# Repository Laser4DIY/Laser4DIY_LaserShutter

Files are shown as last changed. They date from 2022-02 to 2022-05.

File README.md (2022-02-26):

# LASER4DIY Laser Shutter

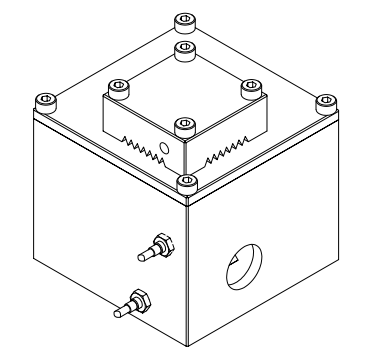
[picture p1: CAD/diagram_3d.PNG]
Laser4DIY Laser Shutter - 3D view

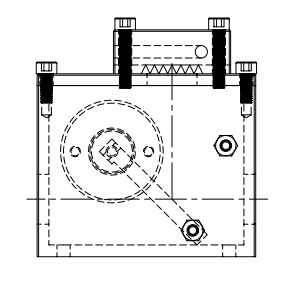
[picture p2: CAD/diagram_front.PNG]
Laser4DIY Laser Shutter - front view


This is the repository is part of the [Laser4DIY project](http://www.laser4diy.org/).

## Description 

The laser shutter was designed for CO2 glass tube laser sources typically used in laser cutters, with a power of no more than 50W. The design includes a beam dump which takes up the laser power when the laser is active but the shutter is closed. The actual maximum power depends on how this block is cooled. Please add a heat sink or - even better - active cooling, depending on your requirements. The shutter lid itself is made of copper which has a high reflectivity at the wave length of ~10µm. For other wave lengths this is design cannot be used.

For a laser shutter to be effective, it has to be integrated into the machine safety concept. The electronics circuit that is included in this documentation can only serve as an example and has to be adapted to your needs.

Please note that this documentation is distributed without any express or implied warranty. Use it at your own risk. Please also read the details of the CERN-OHL license.

## License

This hardware documentation is licensed under CERN-OHL-P v2.

---

Copyright FabLab München e.V. 2021.

Laser4DIY is sponsored by the Federal Ministry of Education and Research

This source describes Open Hardware and is licensed under the CERN-OHL-P v2

You may redistribute and modify this documentation and make products using it 
under the terms of the CERN-OHL-P v2 (https:/cern.ch/cern-ohl).
This documentation is distributed WITHOUT ANY EXPRESS OR IMPLIED WARRANTY, 
INCLUDING OF MERCHANTABILITY, SATISFACTORY QUALITY AND FITNESS FOR A  PARTICULAR 
PURPOSE. Please see the CERN-OHL-P v2 for applicable conditions

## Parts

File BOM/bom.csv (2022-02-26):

No. | Artikel | Hersteller | Bezugsquelle | Bestellnummer | Stk. | Preis (ca) | Summe
1 | Ber hrungsloser Sicherheitsschalter | Pilz | RS Components | 619-2818 | 1 | 60 | 60
2 | PNOZ X3, 2-Kanal Sicherheitsrelais | Pilz | RS Components | 245-1848 | 0 | 220 | 0
3 | PNOZ s3, 2-Kanal Sicherheitsrelais | Pilz | RS Components | 156-083 | 2 | 150 | 300
4 | Drehmagnet D34 | Kuhnke | B rklin | 27G184 | 1 | 140 | 140
5 | PSEN Kabel Gerade | Pilz | Pilz | 533111 | 1 | 10 | 10
6 | Induktiver Sensor Schlieáer IM04-0B6PS-ZU1 | Sick | RS Components | 209-3201 | 1 | 85 | 85
7 | Induktiver Sensor ffner IM04-0B6PO-ZU1 | Sick | RS Components | 209-3198 | 1 | 85 | 85
8 | Shutter Fr steile | custom |  |  | 1 | 200 | 200
 |  |  |  |  |  | Summe | 880

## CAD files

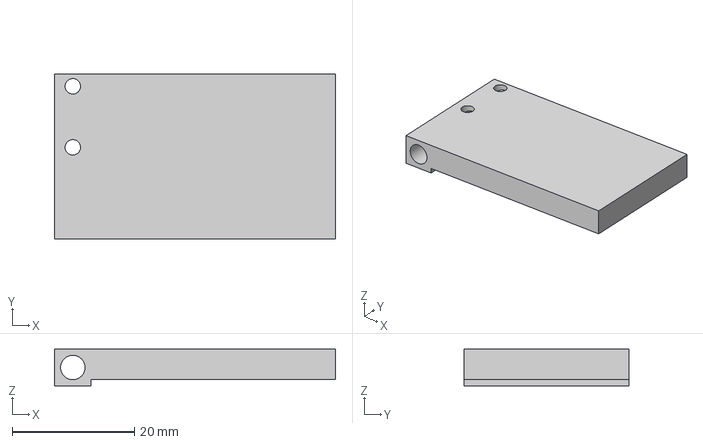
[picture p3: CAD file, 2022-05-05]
CAD/STEP/Fahne.step
46.0 x 27.0 x 6.00 mm

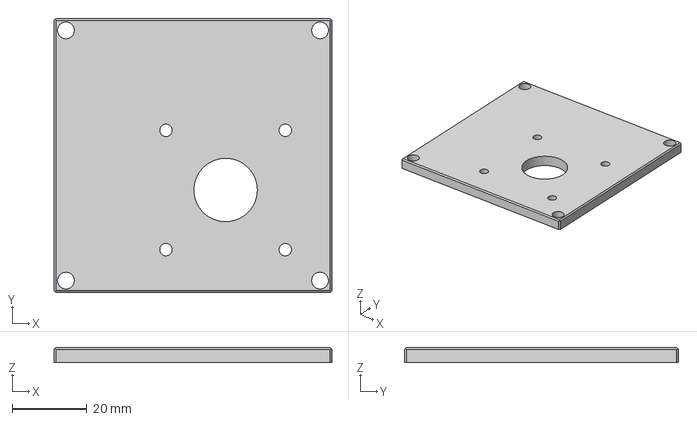
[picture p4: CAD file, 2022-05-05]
CAD/STEP/Deckel.step
74.5 x 73.5 x 4.00 mm

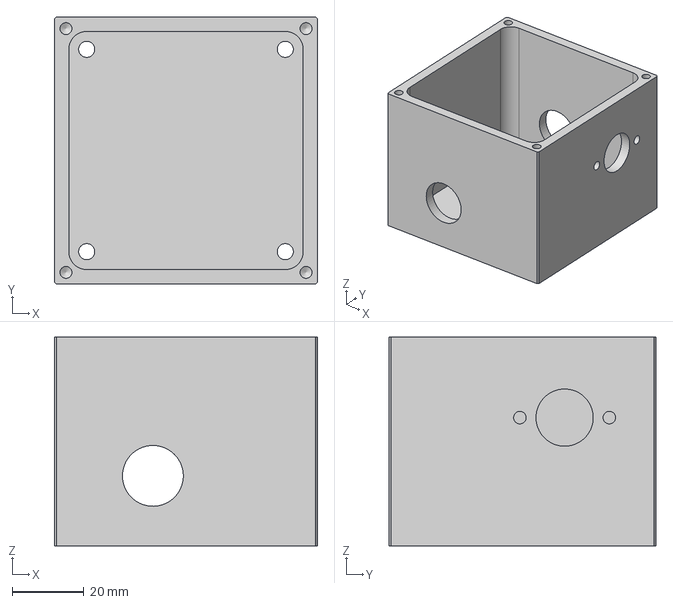
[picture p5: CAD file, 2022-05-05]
CAD/STEP/Gehaeuse.step
73.5 x 74.5 x 58.3 mm

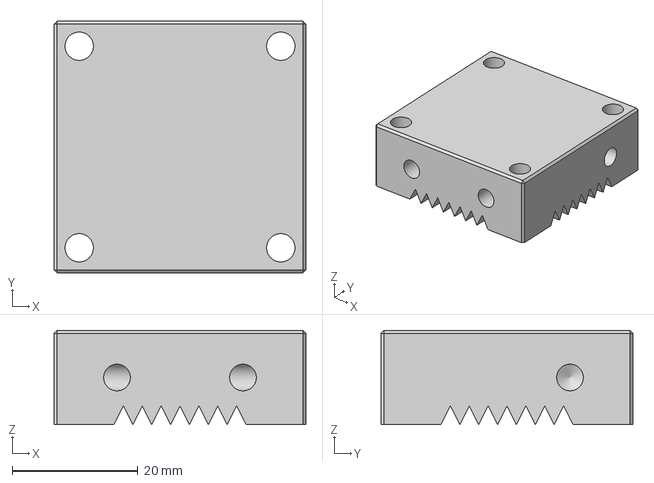
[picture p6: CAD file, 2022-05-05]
CAD/STEP/Kuehlung.step
40.0 x 40.0 x 15.0 mm

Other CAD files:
CAD/Shutter.f3z

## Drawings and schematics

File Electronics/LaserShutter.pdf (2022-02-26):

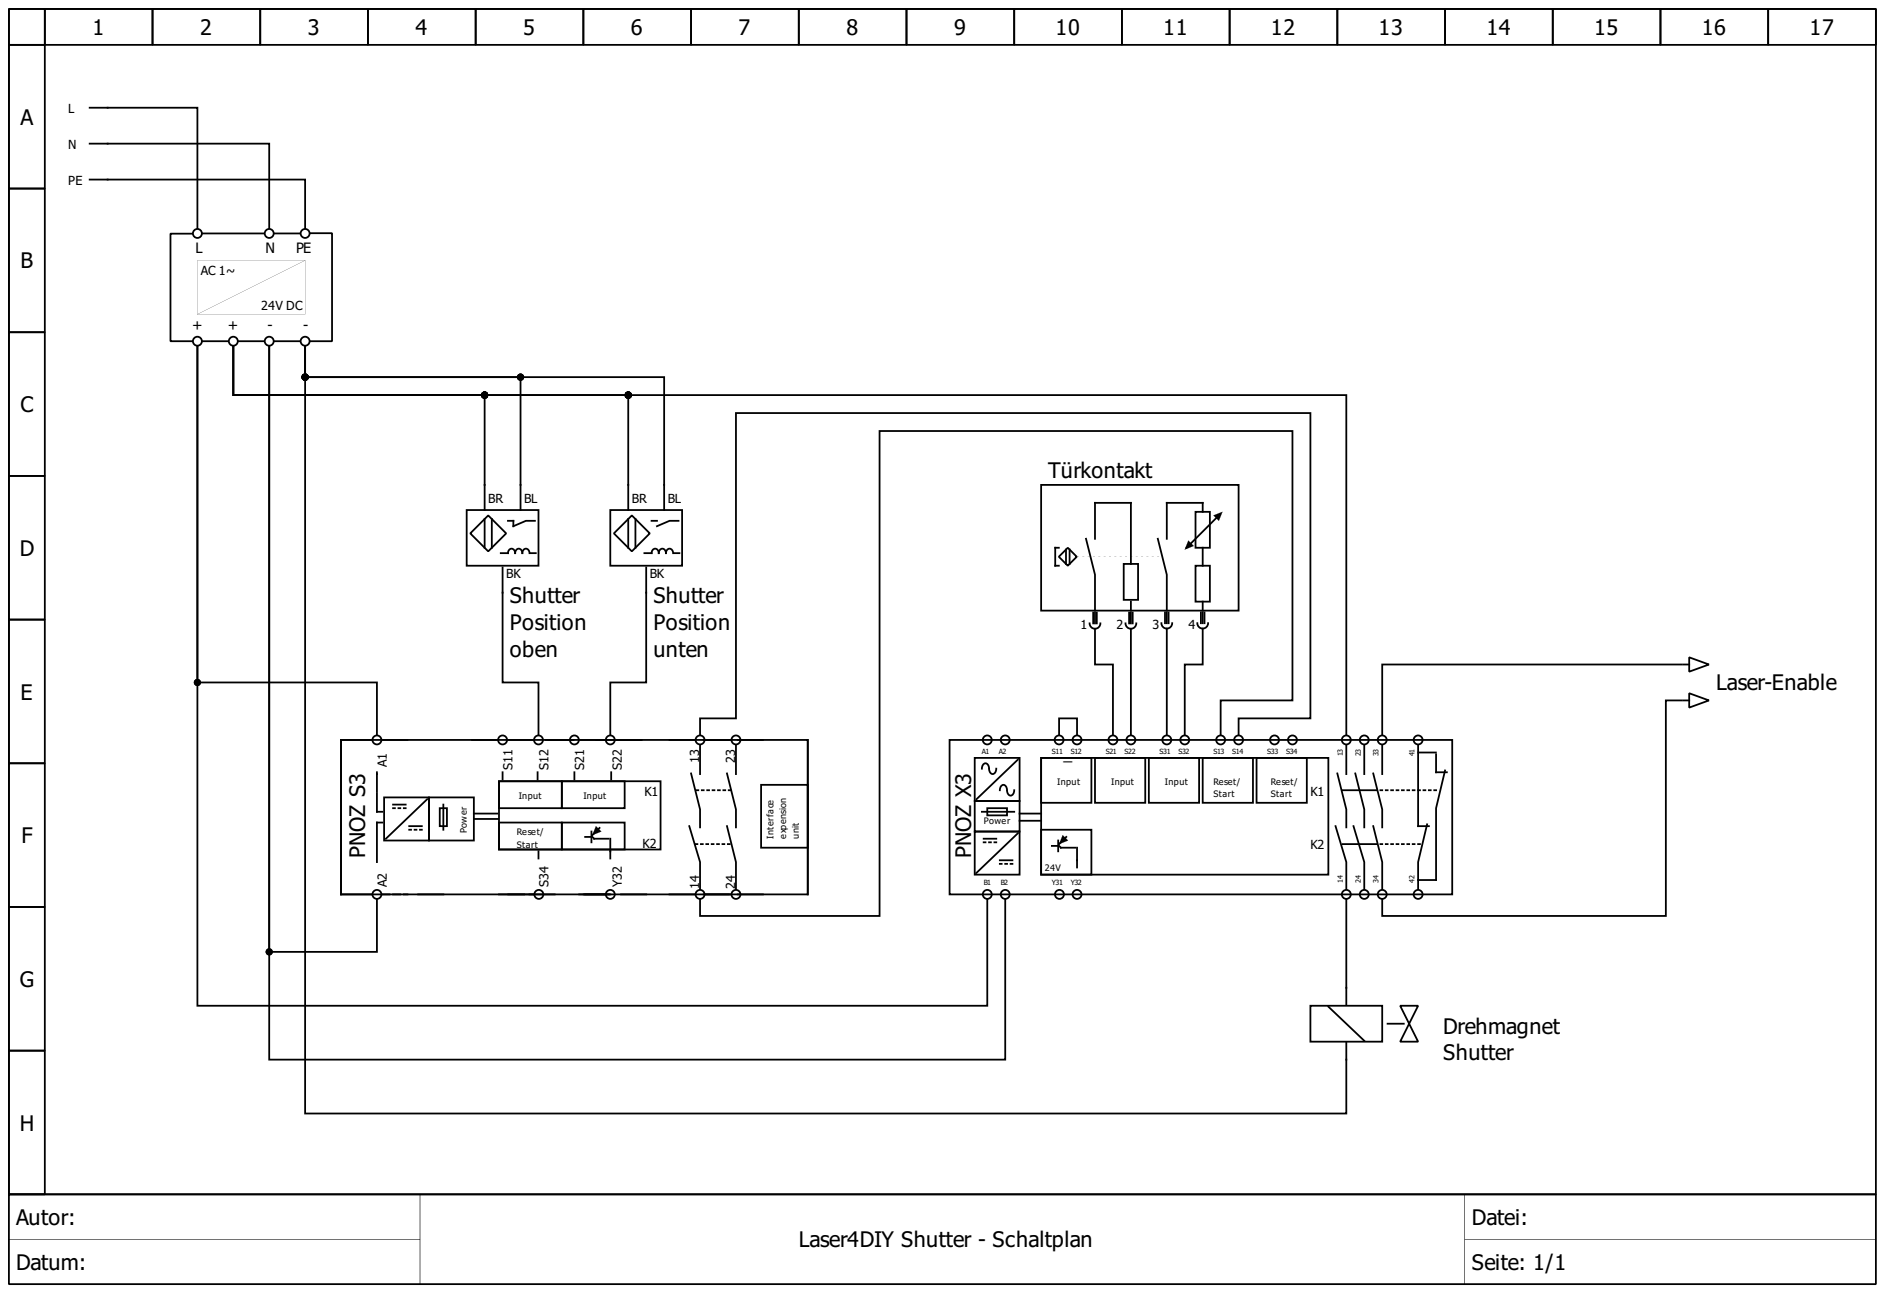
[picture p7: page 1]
Input; Reset/ Start; Interface; expension; unit; Power; Reset/; Start; Drehmagnet Shutter; Türkontakt; Shutter Position unten; Shutter Position oben; Laser-Enable

Autor: | Laser4DIY Shutter - Schaltplan | Datei:
Datum: | | Seite: 1/1

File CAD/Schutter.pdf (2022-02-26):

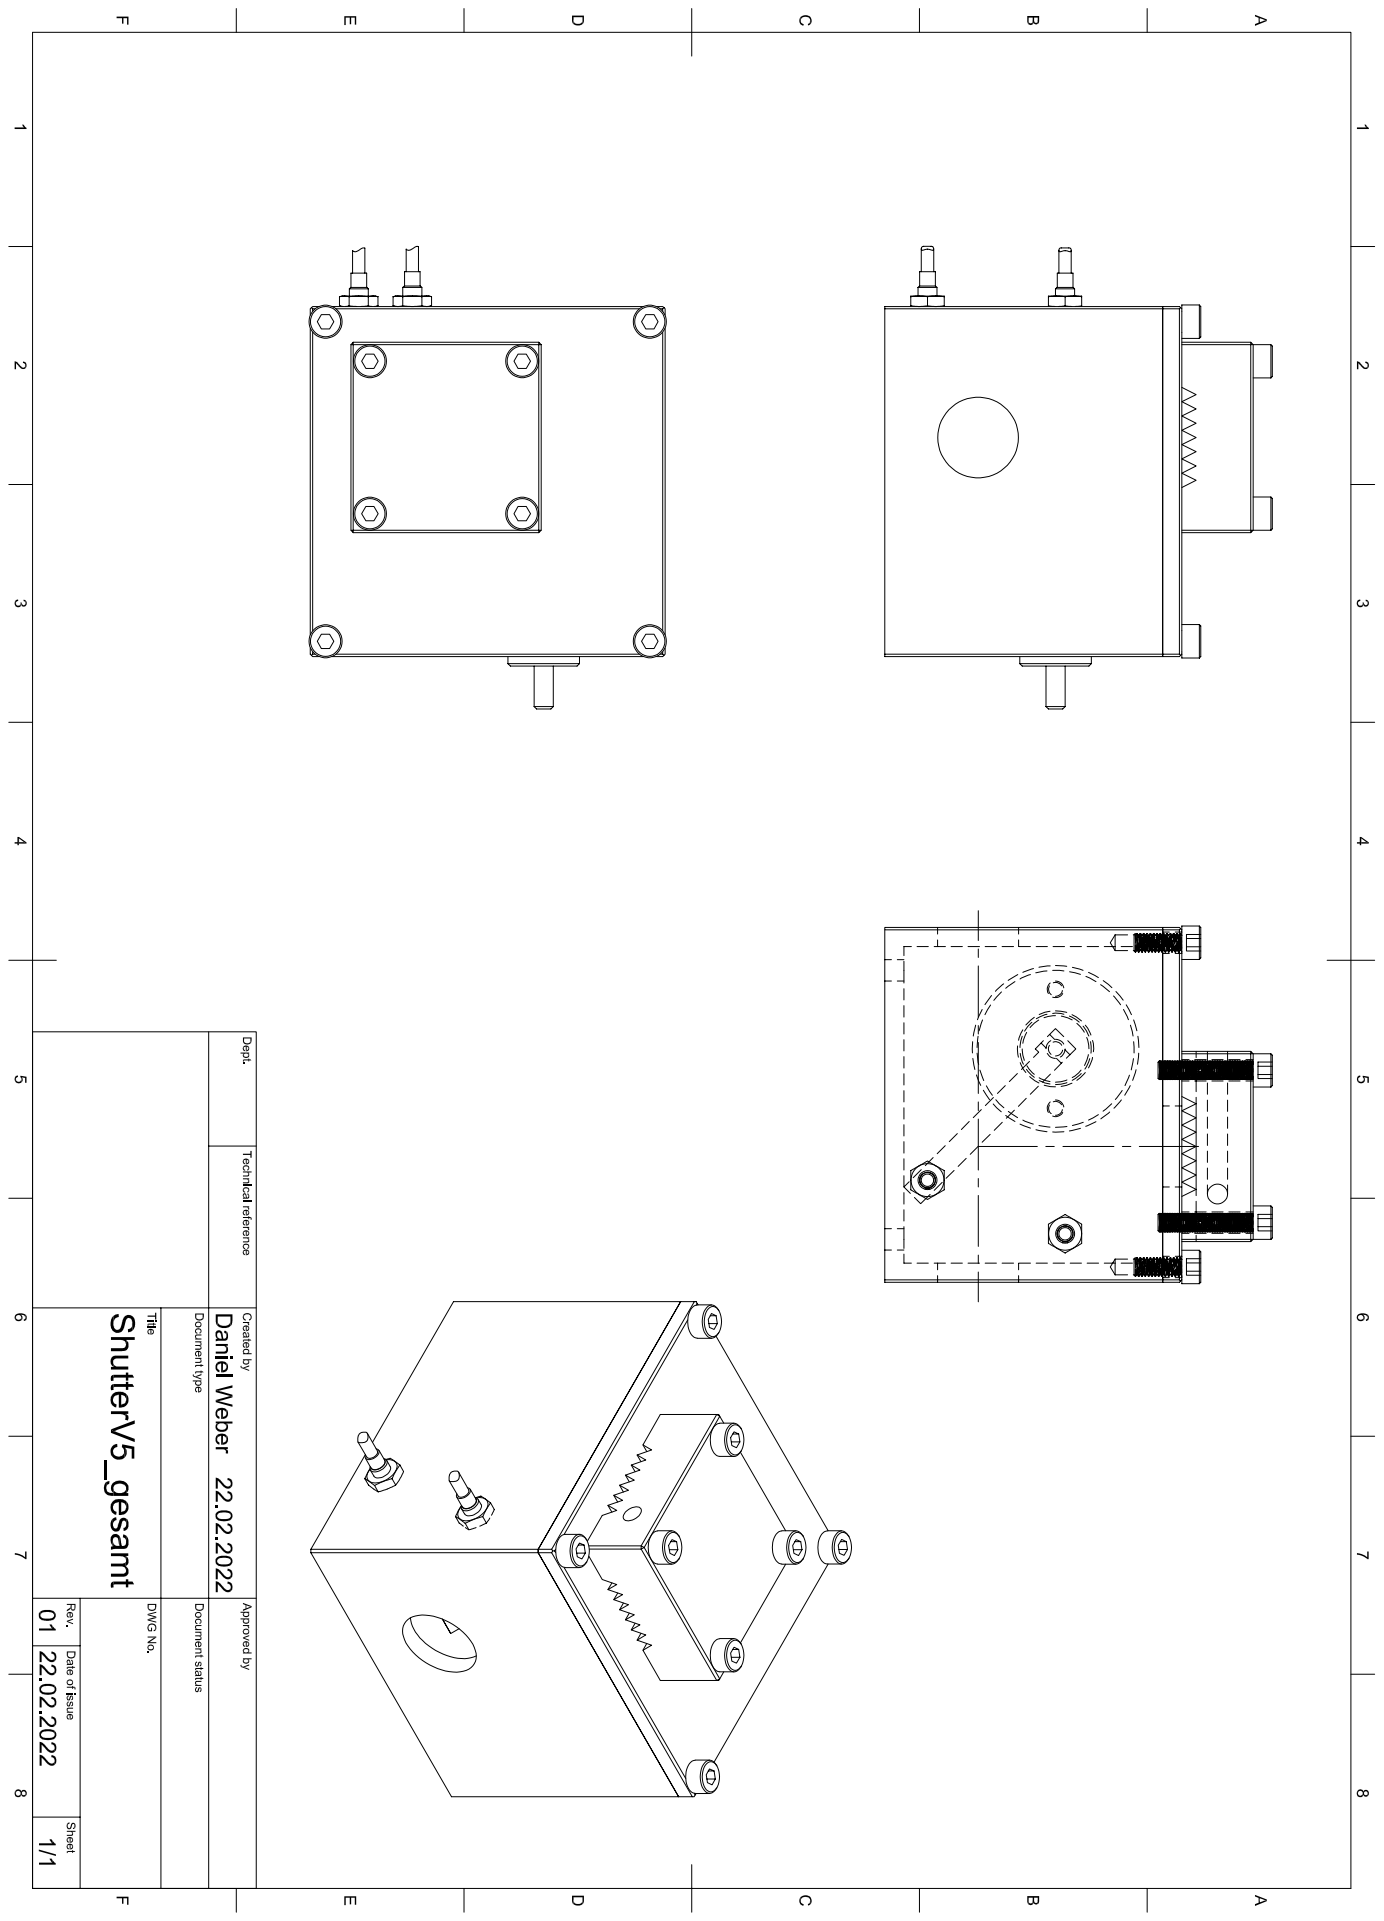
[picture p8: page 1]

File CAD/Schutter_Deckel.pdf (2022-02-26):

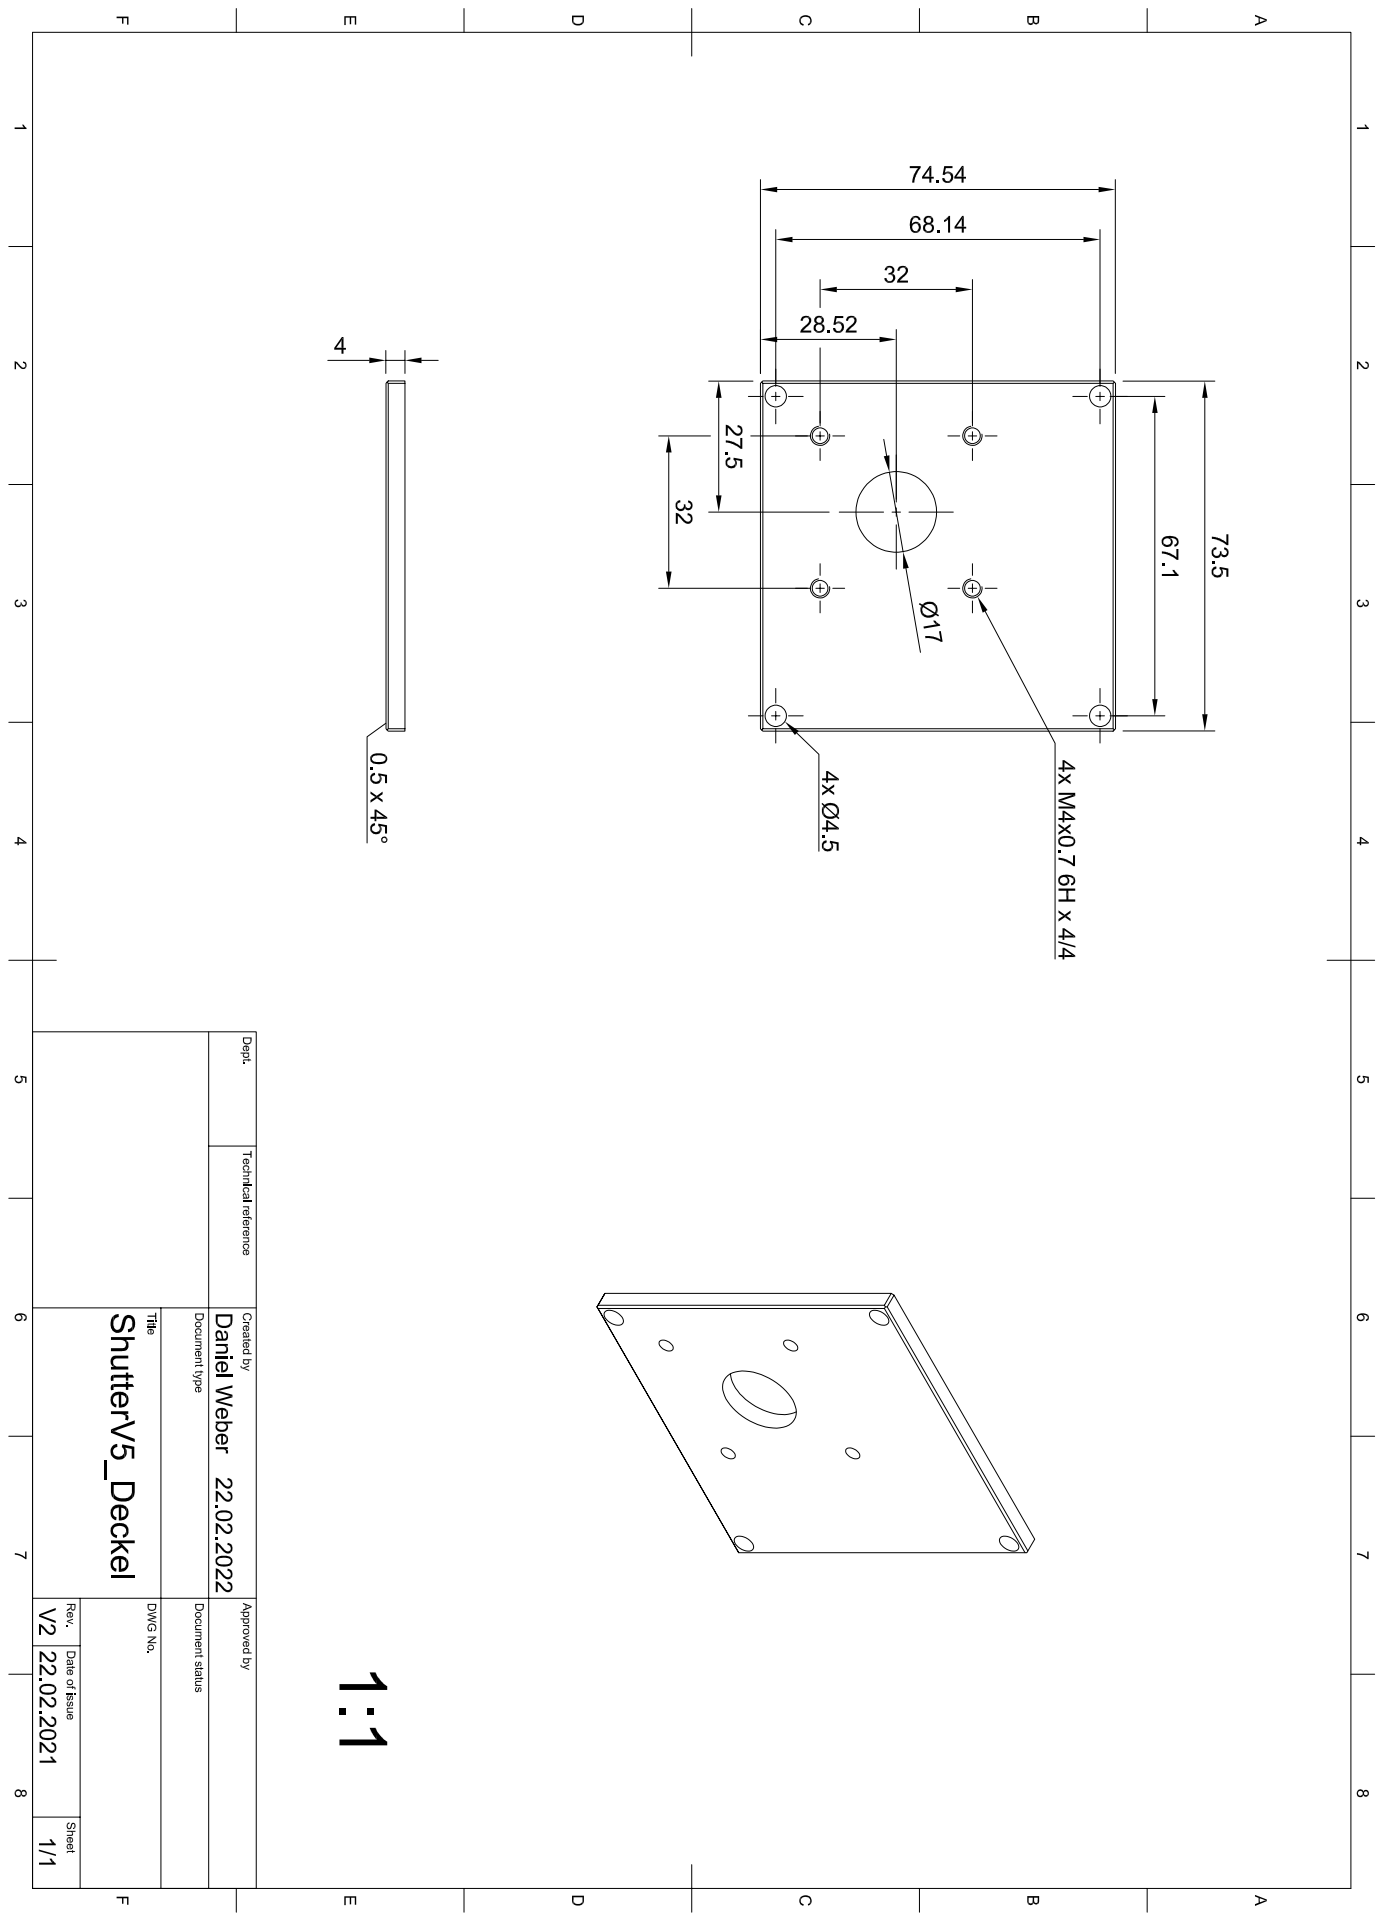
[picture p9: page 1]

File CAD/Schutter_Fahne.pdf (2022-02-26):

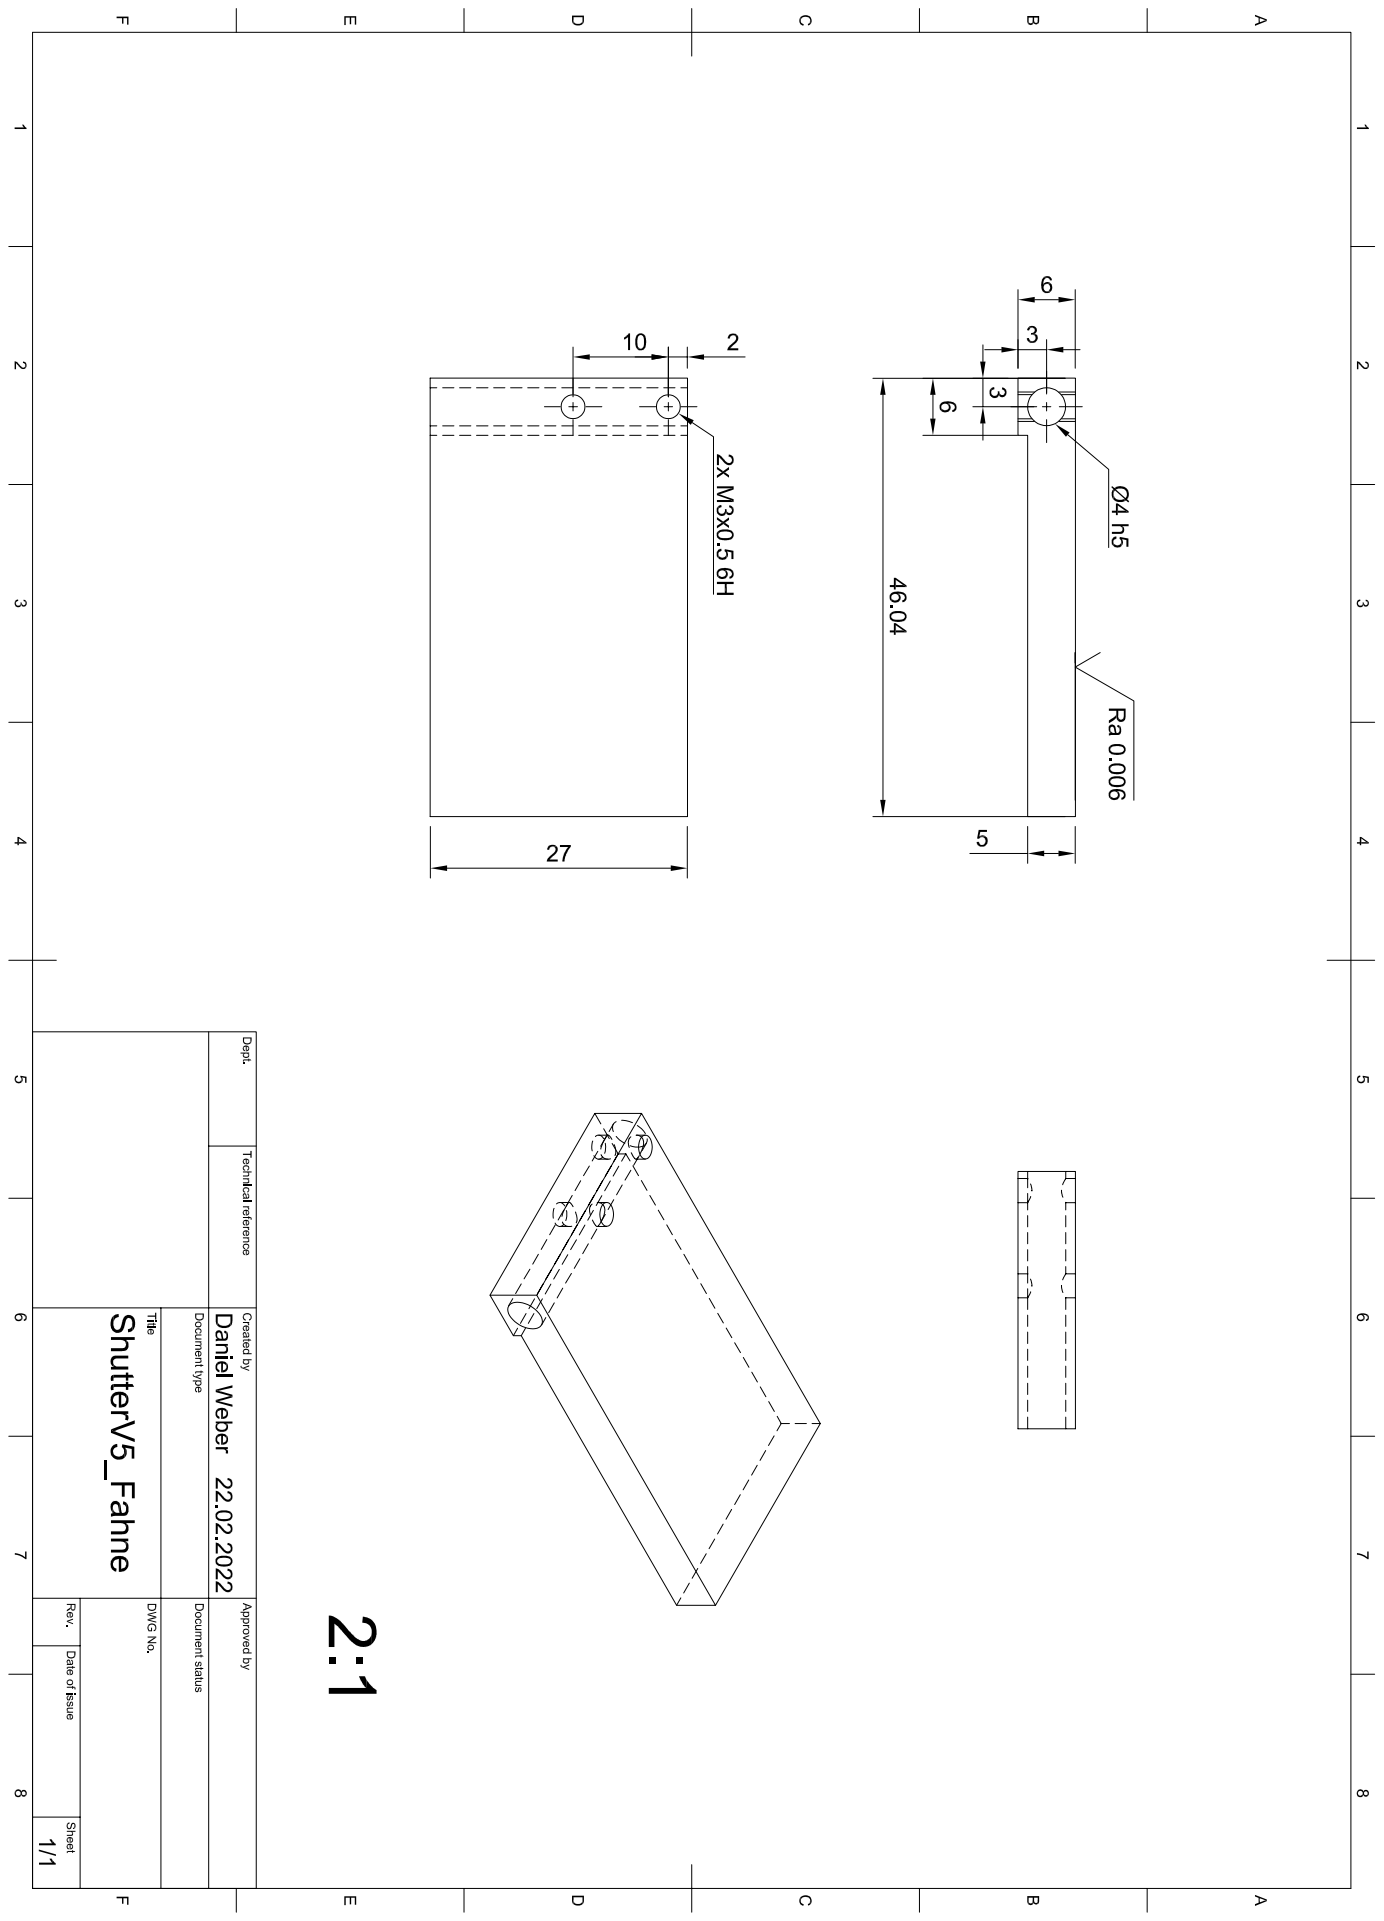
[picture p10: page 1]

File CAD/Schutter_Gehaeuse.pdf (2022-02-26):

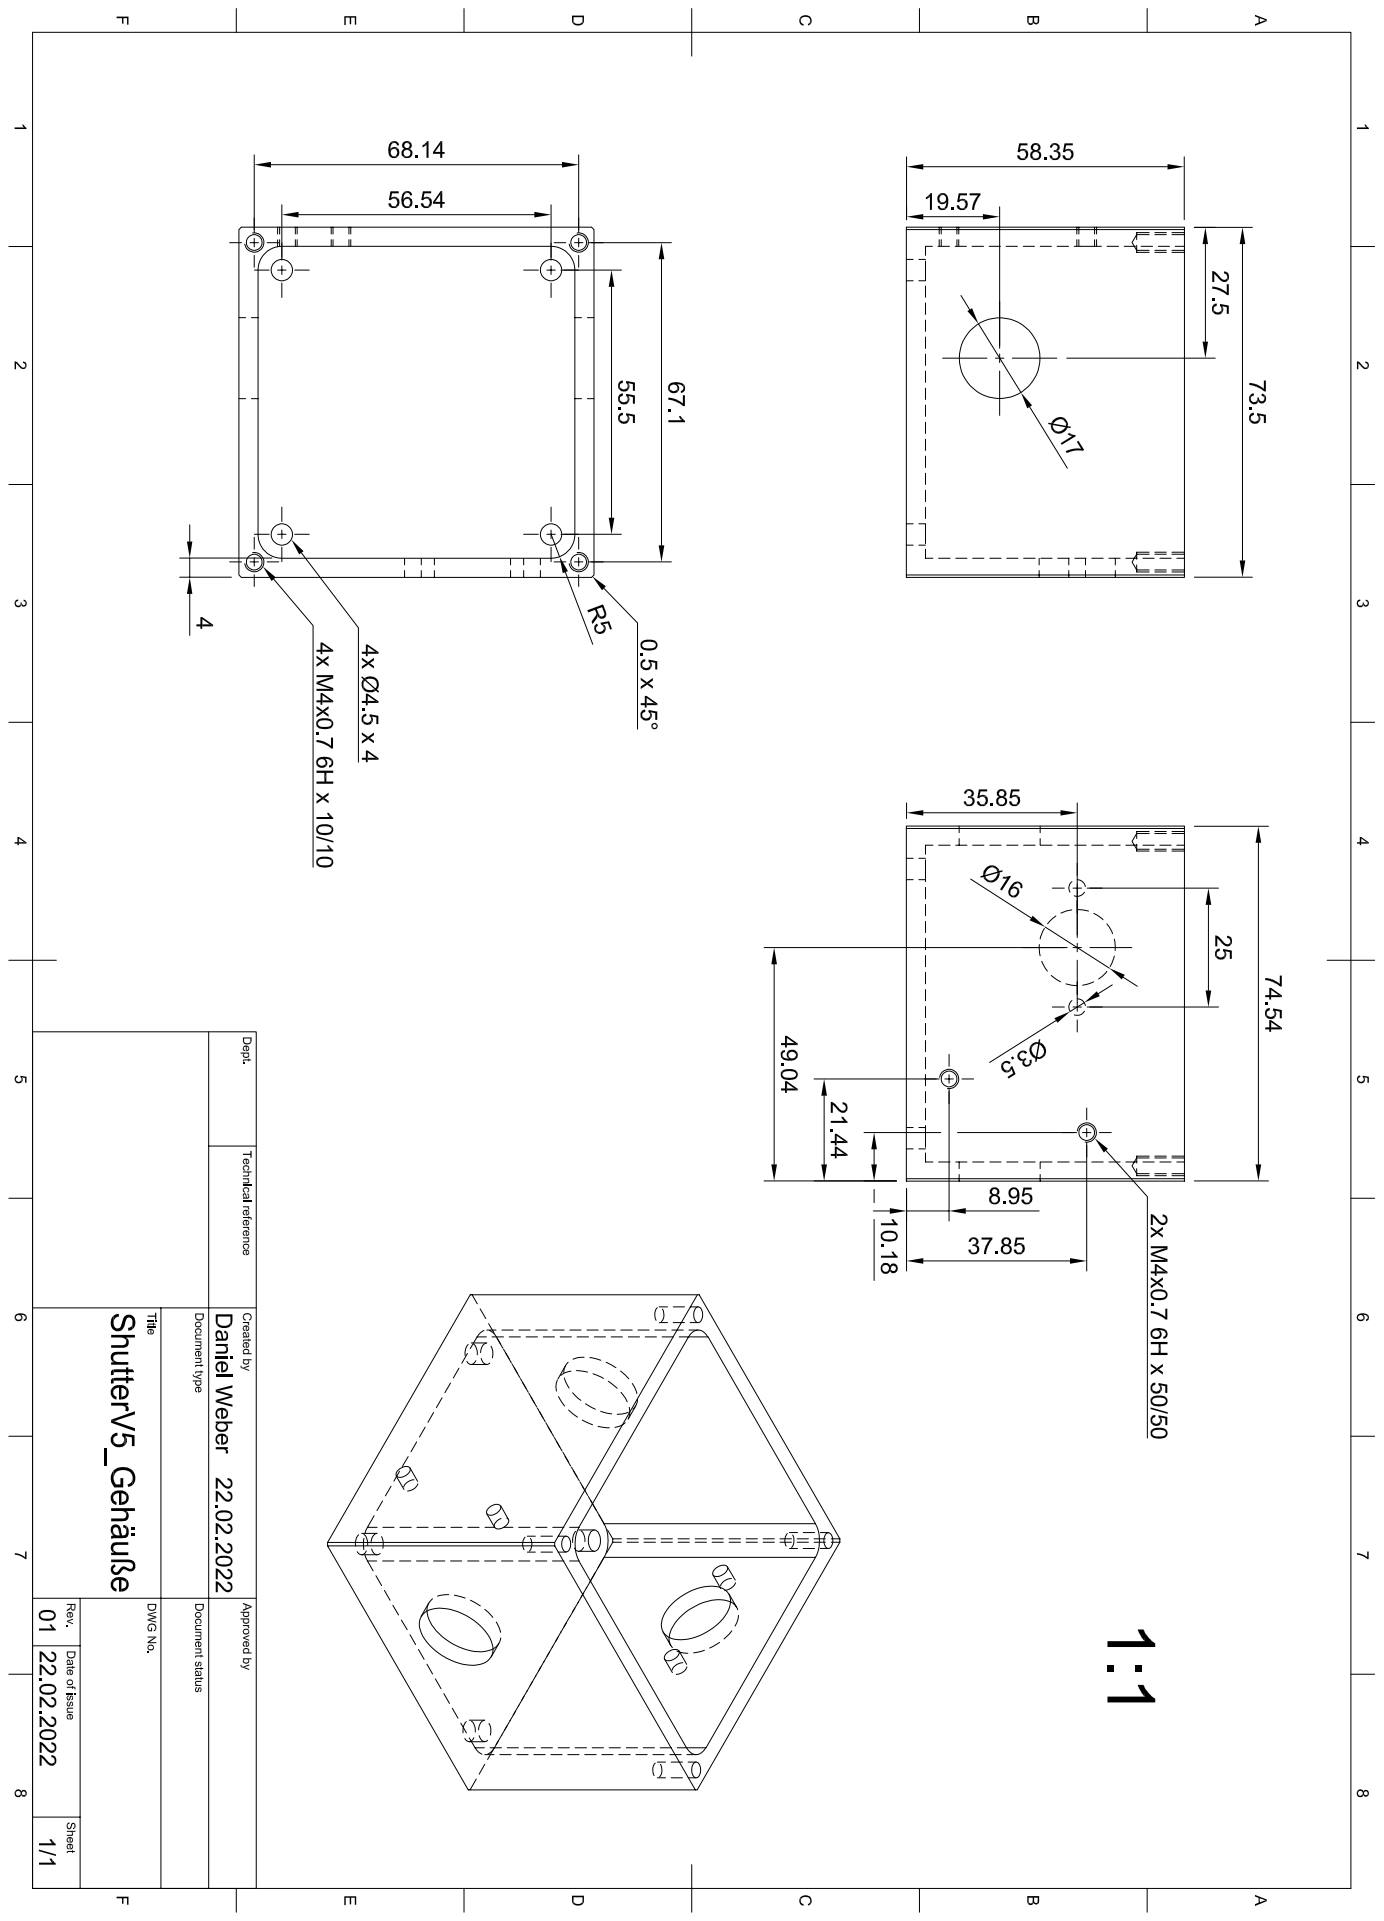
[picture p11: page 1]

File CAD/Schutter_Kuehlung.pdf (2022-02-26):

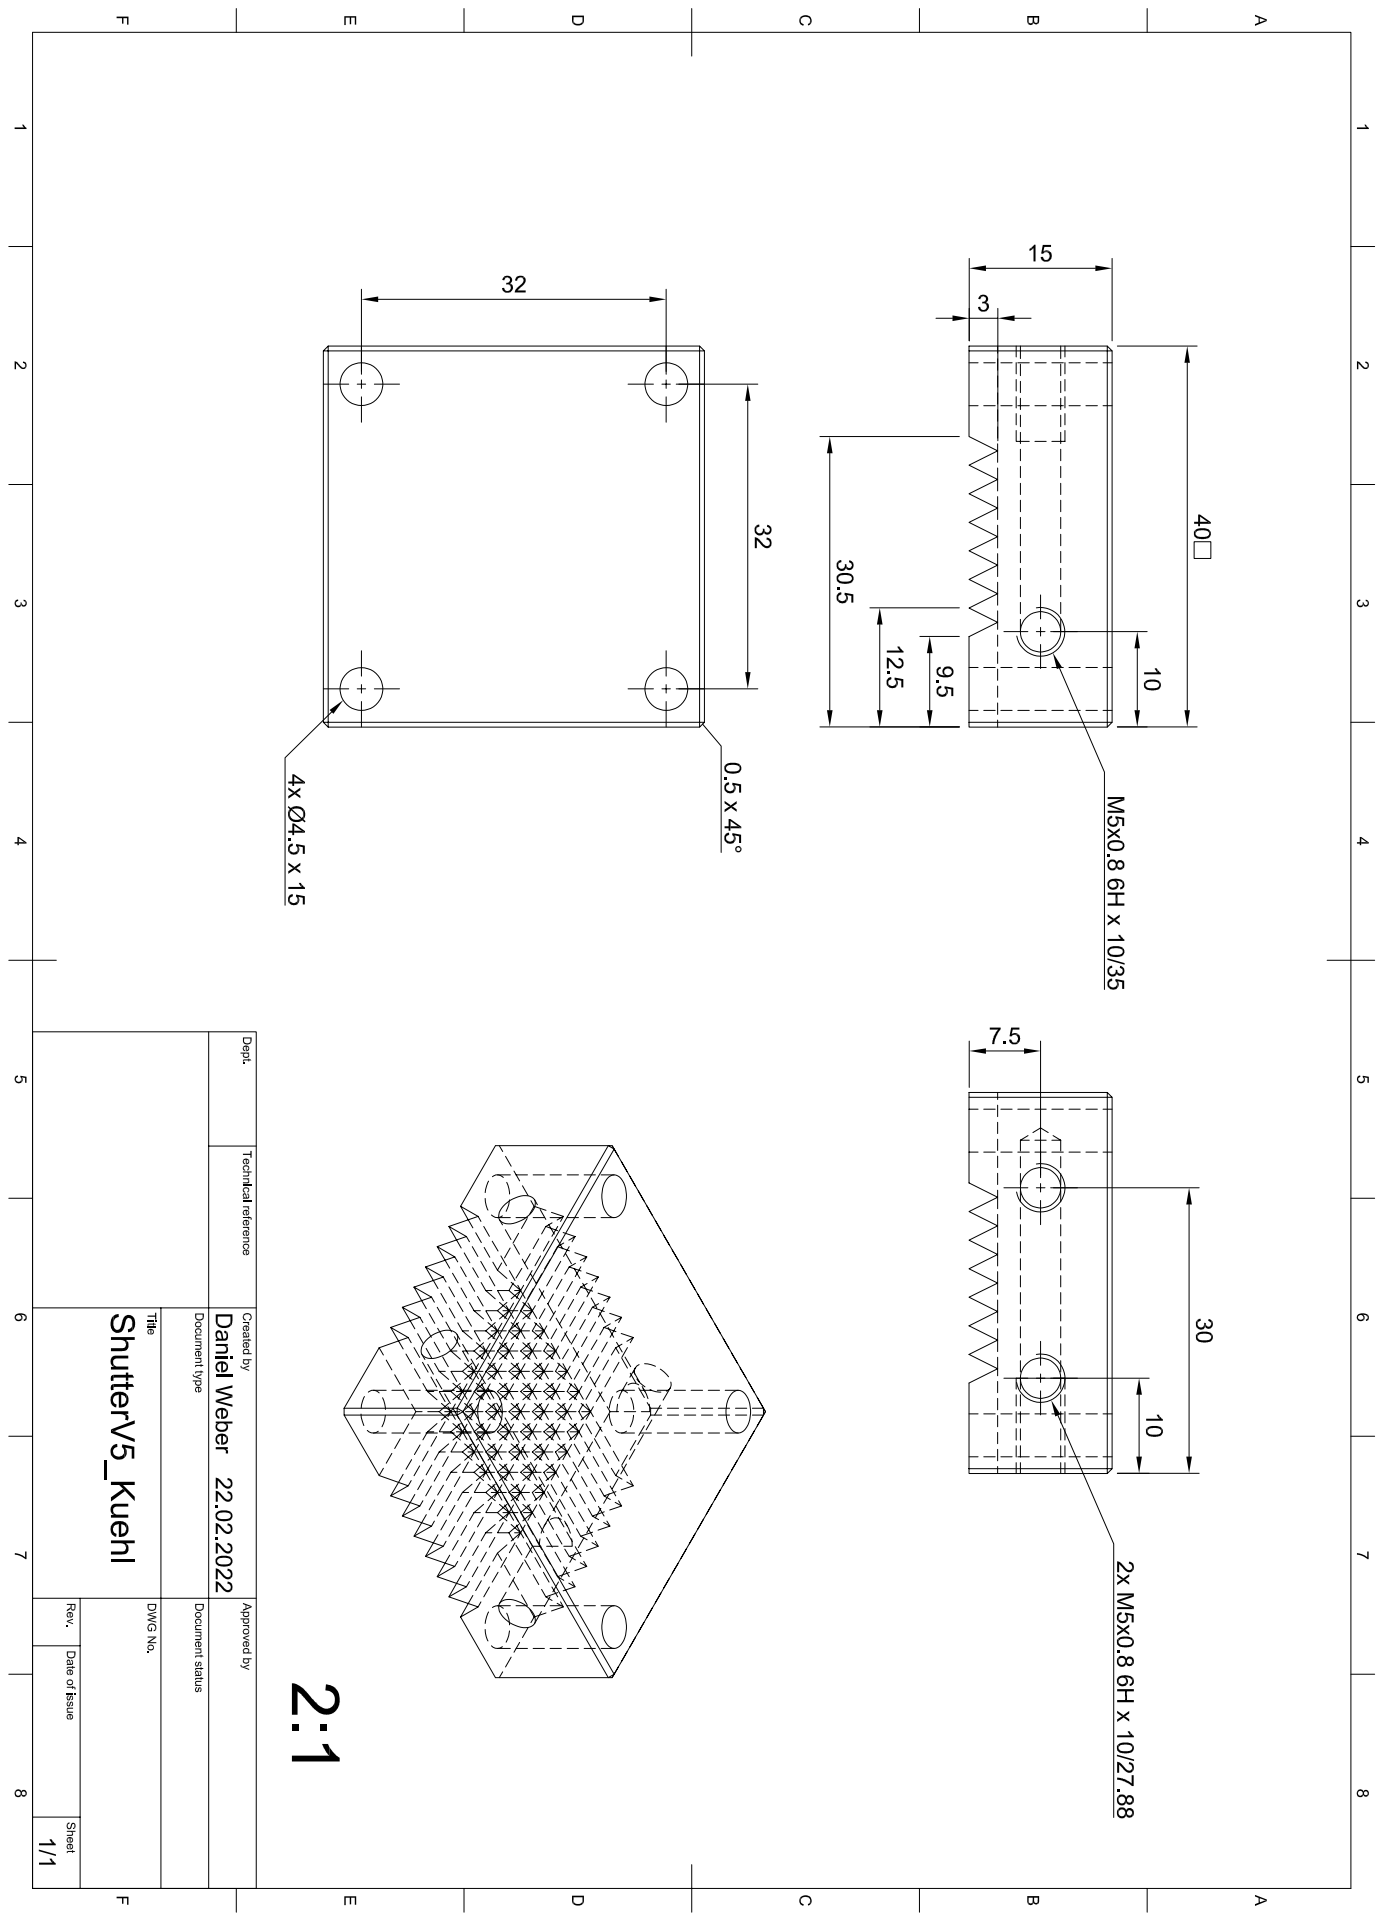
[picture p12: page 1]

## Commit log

2022-02-26 initial import, v5 cad files
    [Shutter.f3z]
2022-02-26 added BOM; Schaltplan
    [bom.csv]
2022-05-05 added STEP files
    [Deckel.step, Fahne.step, Gehaeuse.step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]
